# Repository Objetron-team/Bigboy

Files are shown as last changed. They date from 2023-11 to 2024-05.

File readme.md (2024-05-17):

# The Big boy
[Eurobot](https://www.coupederobotique.fr/wp-content/uploads/Eurobot2024_Rules_CUP_EN_FINAL.pdf)

## Mission
- Repot the plants and place them in cultivation
- Orient the solar panels
- Pollinate the plants
- Return to charge batteries
- Anticipate future crop yields

## Rules highlight
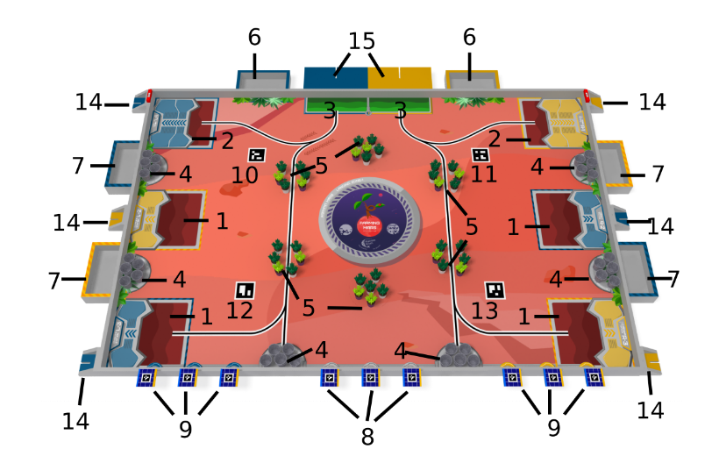
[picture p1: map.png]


|||
|-|-|
| 1) Departure/arrival and drop-off areas | 8) Solar panels |
| 2) Departure/arrival and reserved drop-off areas  | 9) Reserved solar panels |
| 3) Departure areas SIMA (ladybug hive) | 10) ArUco marker number 20 |
| 4) Pot supply | 11) ArUco marker number |
| 5) Plant supply | 12) ArUco marker number 22 |
| 6) Reserved planters | 13) ArUco marker number 23 |
| 7) Planters | 14) Fixed beacon supports |
| | 15) Remote computing area |

## Strategy

### Positionning

#### Bigboy
- Bigboy will be positioned in the departure area in a defined position.
- Bigboy will use its encoders to know its position.
- The mouvement will be determine by the system of tasks.

#### Ladybirds
- Ladybirds will wait for the Bigboy to send a signal to start moving.

### Plants

#### Storage
- Plants will be stored in the storage area of the robot.

#### Open/Close the claw
- Bigboy will open and close its claw to take/let plants in its storage area.
- The claws will be controlled by servo motor.

### Solar
- Not done in this project

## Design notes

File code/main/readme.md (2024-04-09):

# How does it work?

The robot has a BT module, we have encodded a series of actions.

```
b -> select the blue team
y -> select the yellow team

z -> start the sequence
s -> stop the sequence
n -> next move
```

Diagram

Diagram

The sequence is a predefined list of coordinate, a path is generated by a list of forward and rotation mouvement. The position of the pami is managed by two PID controller, for the distance made by the pami and its rotation. We can compute a target speed using the PIDs and the speed is fed to speed PID controller.
The pami stop when the goal is achieved or if an object is detected.

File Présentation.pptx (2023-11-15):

## Objetron

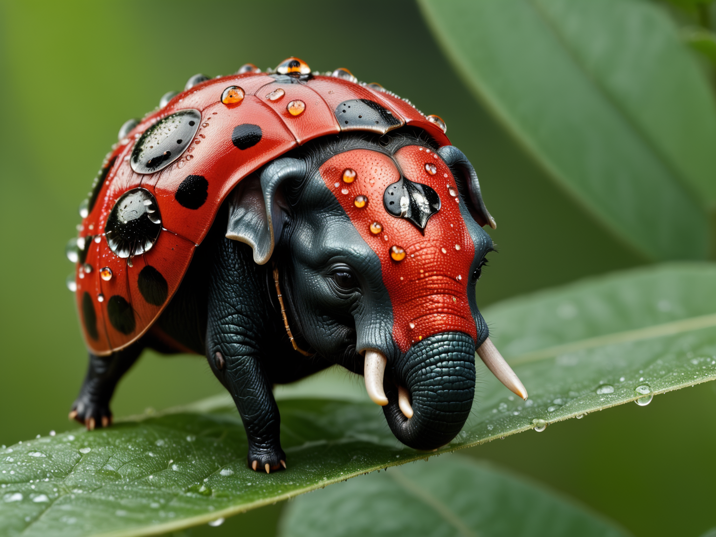
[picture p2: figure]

Florian Lebecque
Régis Irankunda
Rayhan Mezghani
Lancelot Neirinckx
Mathieu Surquin
Adrian Szydlowski

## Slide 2

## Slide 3

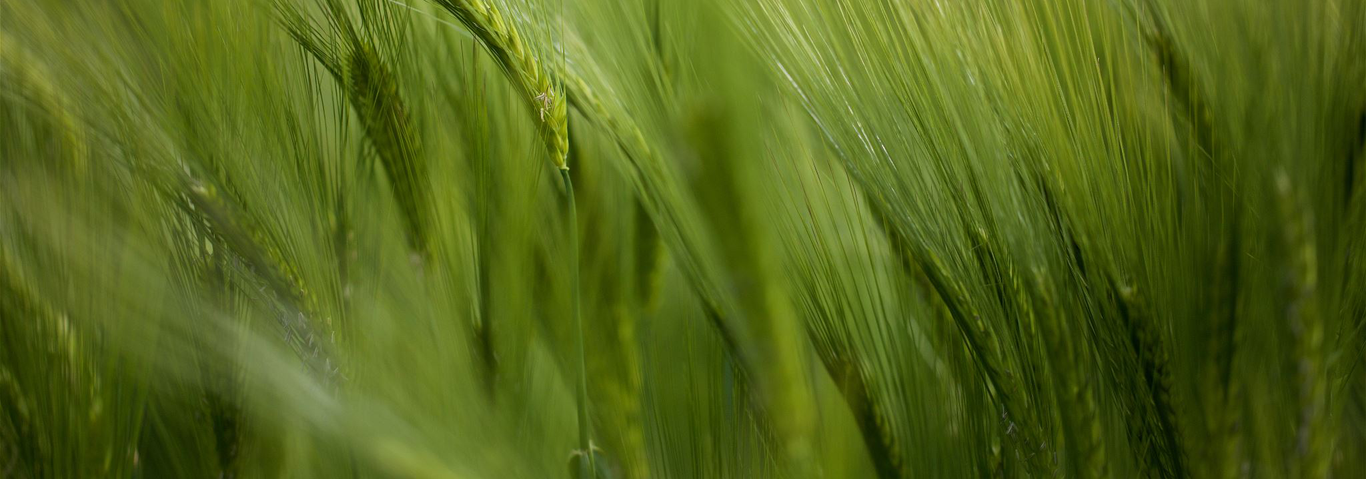
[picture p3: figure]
Gros plan d’orge dans la nature

Comment récolter et identifier les plantes

- Un système de courroie porteuse pour garder les plantes sur le robot
- Le robot identifie les plantes grâce à des capteurs RFID
- Les plantes sont stocker dans des zones différentes sur le robot selon leur type
- Mise en pot des plantes sera effectué sur le robot

## Stratégies

- Récolter plantes zone 5
- Récolter pots zone 4
- Identifier la plante
- Si 1 on prend plante fou dans le pot into zone commune
- Si 2 on prend la plante dans le pot into zone reservée
- Panneau solaire reservé, orientation avec un système de tige
- Panneau solaire non reservé, kinnect observation
- => en fonction du nombre de points
- 90s
- => Robot rentre à la zone de recharge
- => lancement des coccinelles

## Hardware

- Kinect xbox360
- Rails
- Moteurs
- Rasbery, Arduino
- Servo moteur
- Capteur rfid
- Roues
- Carte wifi ou arduino integré ESP32

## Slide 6

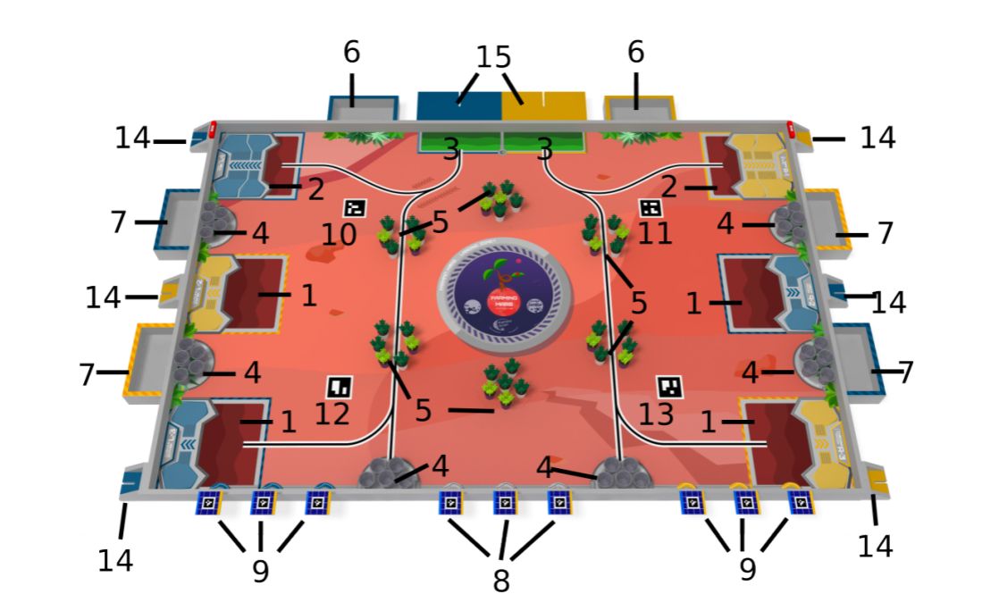
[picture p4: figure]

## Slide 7

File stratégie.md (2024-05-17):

# Stratégie EUROBOT
Dans ce document, nous allons décrire la stratégie de notre robot afin de ramener le plus de points possibles. La stratégie de notre robot peut se décomposer selon les étapes qui suivent.

## Plantes
La première étape va consister à la récolte des plantes. Bigoy démarre de la zone 1 pour l'équipe jaune ou zone 2 pour l'équipe bleue il ira ensuite rechercher les stocks de plantes afin de les emmener dans la zone de dépôt (1 et 2). Seules les plantes résistantes seront valides dans ces zones, et une plante dans la bonne zone donne 3 points.
=> 3*(2+2) = 12pts
### Plantes bonus
Le robot ira ensuite récuperer si possible les plantes du milieu de terrains et celles de l'adversaire si elles n'ont pas été touchées
=> 3*(2+2+2) = 18pts

## Panneaux solaires
Les panneaux solaires ne sont pas compris dans notre stratégie.

## PAMIS
L'étape suivante est attribuée aux PAMIs. À la 90ème seconde, les PAMIs entreront en contact avec une plante dans la zone de dépôt en moins de 10 secondes. Un PAMI qui est dans une zone de dépôt ramène 5 points, et s'il est en contact avec une plante, il rapporte 5 points de plus.
=> 5+5 = 10pts

## Retour à la base
À la fin de la manche, le robot retourne à sa zone de charge du coté adverse. Cette action donne 10 points.
=> 10 pts

## Affichage dynamique
Une dernière manière de marquer des points est de pouvoir prédire le score que le robot va faire durant le match. Nous avons décidé de le faire de manière dynamique via un écran OLED. À chaque tâche effectuée, le score s'incrémentera tout seul. Les points attribués pour cela sont donnés selon la formule suivante min(20-écarts/2; points réalisés).
=> 20 pts

## Conclusion
Bigboy et nos PAMIs utiliseront le même code avec le système de tâche. La détection de collision se fera à l'aide de capteurs ultrasons.
Si tout se passe comme prévu, nous devrions idéalement marquer 70 points.

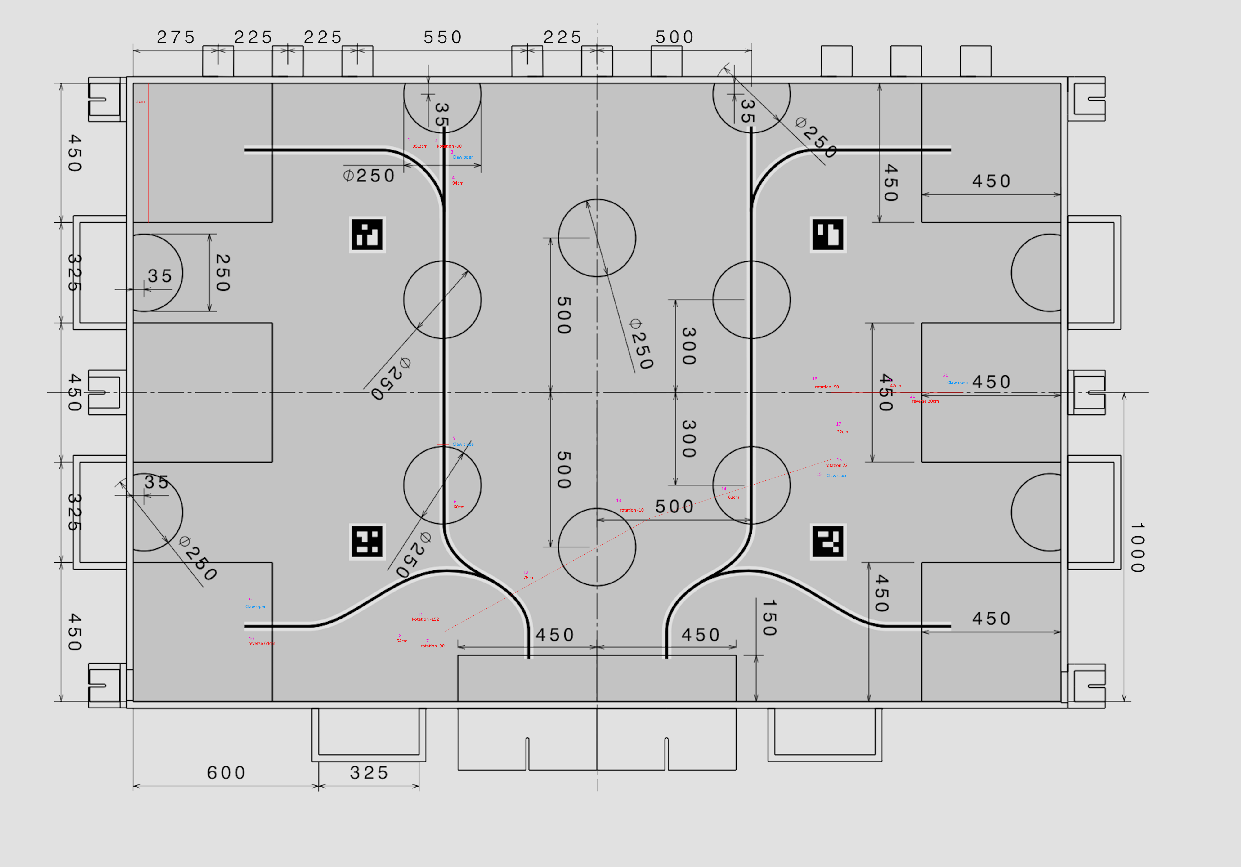
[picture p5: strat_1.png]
Map


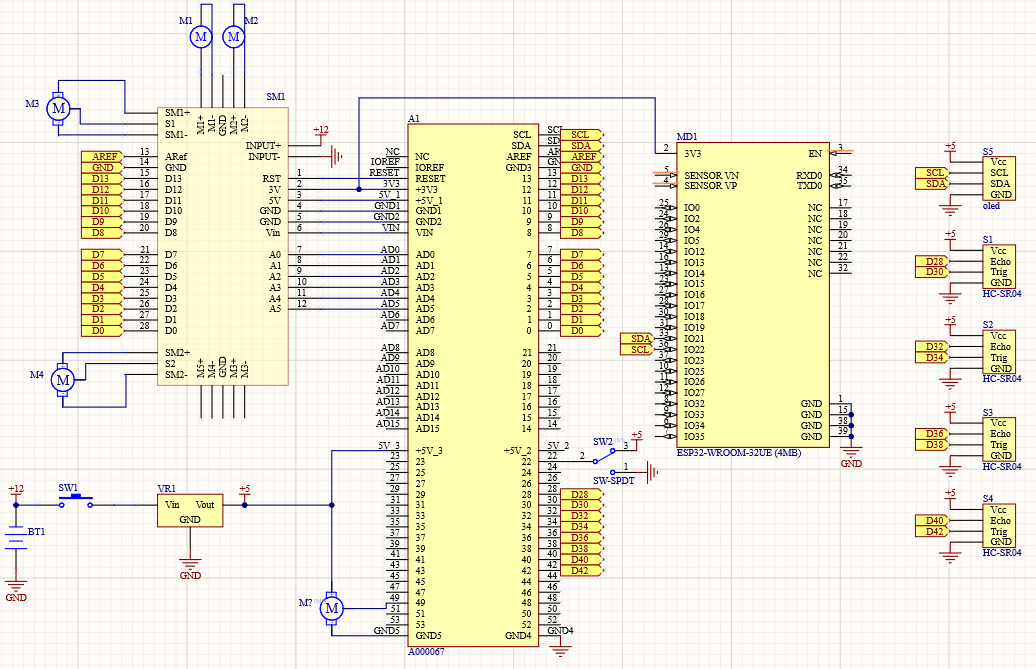
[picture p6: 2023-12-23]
electric_scheme.png

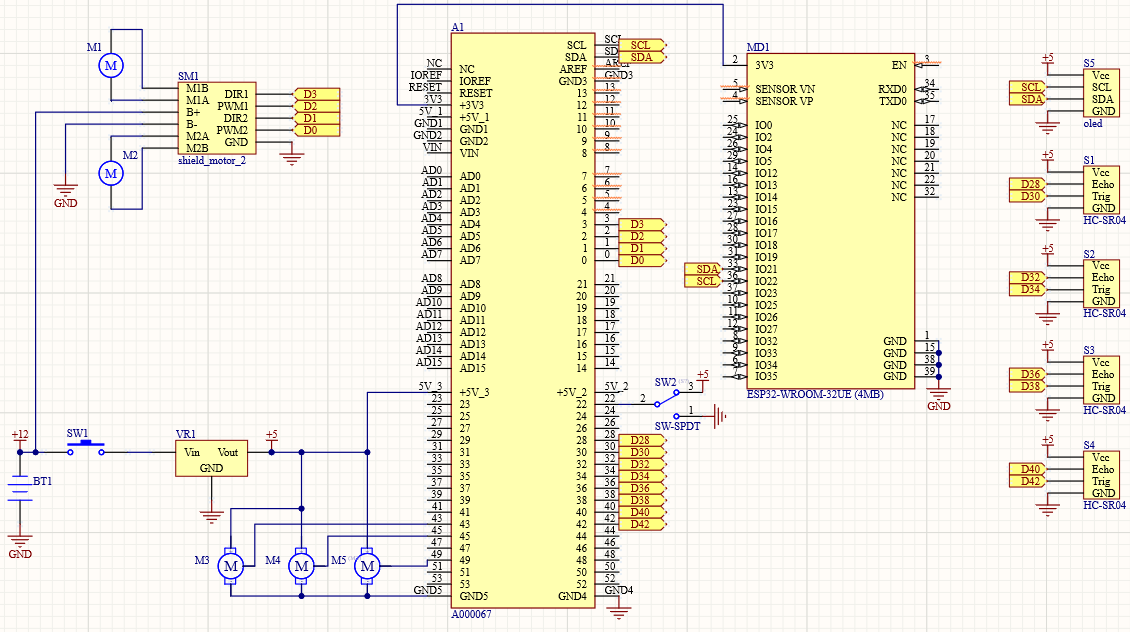
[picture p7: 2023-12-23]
electric_scheme_2.png

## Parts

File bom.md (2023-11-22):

# Bil of materials

## Miscellaneous

|Element|Name|target|Qty|Price|Link|
|-|-|-|-|-|-|
|Urgent stop| - | Lady + Big boy |4| - | - |
|Switch| 2 position | Lady + Big boy |4| - | - |

## Drive system

|Element|Name|target|Qty|Price|Link|
|-|-|-|-|-|-|
|Motor| moteur coci |Lady + Big boy|8|2.77€|https://fr.aliexpress.com/item/1005006027063973.html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|
|Chenilles|Zodiac MX8 MX6 Baracuda R0526100|Big boy|1|18.99€|https://www.amazon.fr/Chuancheng-Piscine-Zodiac-Baracuda-R0526100/dp/B07WZZRPDM|
|Encoder|LM393 Infrared Optocoupler Speed Sensor Module|Lady + Big Boy| 8|0.35|https://electropeak.com/ptocouple-optocounter-module

## Collision system

|Element|Name|target|Qty|Price|Link|
|-|-|-|-|-|-|
|Capteur Ultrason| HC-SR04 | Lady + Big boy |7|5.61€|https://www.mouser.be/ProductDetail/OSEPP-Electronics/HC-SR04?qs=wNBL%252BABd93PqZEhuhHkuOw%3D%3D|

## Solar rotator

|Element|Name|target|Qty|Price|Link|
|-|-|-|-|-|-|
|Servo motor| - | Big boy | 1 | - | - |
|Motor| - | Big boy | 1 | - | - |

## Beacon tower

|Element|Name|target|Qty|Price|Link|
|-|-|-|-|-|-|
|Raspberry| - | Beacon | 1 | - | - |
| Camera | - | Beacon | 2 | - | - |

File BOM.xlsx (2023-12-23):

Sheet: Sheet1
Element | Nom | Prix | Lien | Qnt
Capteur ultra-son | HC-SR04 | 5.61 € | https://www.mouser.be/ProductDetail/OSEPP-Electronics/HC-SR04?qs=wNBL%252BABd93PqZEhuhHkuOw%3D%3D | 7
Moteur cocci |  | 8.02 € | https://fr.aliexpress.com/item/1005006027063973.html?curPageLogUid=bDT0fOmhaEm0 | 1
servo-moteur |  |  |  | 2
moteur | GA12-N20 + encoder | 6 € | https://nl.aliexpress.com/item/1005004999529855.html | 8 | https://nl.aliexpress.com/item/1005002439195511.html?scm_id=1007.40050.362094.0&scm-url=1007.40050.362094.0
capteur anti-collision | VL53l0x |  | https://nl.aliexpress.com/item/1005006177829793.html?
Bouton d'arrêt d'urgence |  |  |  | 4
Switch |  |  |  | 4
Caméra |  |  |  | 1
raspberri pi |  |  |  | 1
Ecran LCD
Paire de chenilles | Zodiac MX8 MX6 Baracuda R0526100 | 18.99 | https://www.amazon.fr/Chuancheng-Piscine-Zodiac-Baracuda-R0526100/dp/B07WZZRPDM | 1 | 2.00 € | https://fr.aliexpress.com/item/1005006054487449.html?src=google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
Encodeur | LM393 Infrared Optocoupler Speed Sensor Module | 0.35 | https://electropeak.com/ptocouple-optocounter-module
 |  | €0.94 | https://fr.aliexpress.com/item/1005002105728736.html?scm_id=1007.40050.362094.0&scm-url=1007.40050.362094.0
Servo |  | 19.35 | https://befr.rs-online.com/web/p/servo-motors/7813046

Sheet: BigBoy
Elément | Nom | Quantité | Prix unité | Notes | Lien
Moteur + encodeur | JGB37-520 | 2 | 4 € | 12V, 1000 rpm, avec support (bracket) | JGB37-520 moteur à courant continu 6V12V avant et barrage vitesse réglable 6 tr/min-1590 tr/min kit de voiture intelligente avec roues - AliExpress (https://fr.aliexpress.com/item/1005005952624823.html?curPageLogUid=67h9Q2mkFTMm)
Capteur ultra-son | HC-SR04 | 4 | 5.61 € |  | https://www.mouser.be/ProductDetail/OSEPP-Electronics/HC-SR04?qs=wNBL%252BABd93PqZEhuhHkuOw%3D%3D
Bouton arret urgence |  | 1 |  | Fourni par le professeur
Batterie | LiPo 3S | 2 | 29 € |  | https://www.conrad.be/nl/p/tattu-lipo-accupack-11-1-v-2300-mah-aantal-cellen-3-45-c-softcase-xt60-1542437.html
5V buck converter | MINI560 | 1 | 1.13 € | PRO-5V | https://nl.aliexpress.com/i/1005001768198398.html?gatewayAdapt=glo2nld
Carte arduino | Arduino Mega | 1 | 45.01 € |  | https://www.mouser.be/ProductDetail/Arduino/A000067?qs=gMoqXxk%2F%2F5apEOlL63oO8Q%3D%3D
Shield moteur | L293D Motor shield | 1 | 6.99 € |  | https://www.amazon.fr/DollaTek-Shield-Expansion-Arduino-Duemilanove/dp/B07DK4NHRW
Carte raspberry pi | Raspberry Pi 4 | 1 | 32.55 € |  | https://www.mouser.be/ProductDetail/Raspberry-Pi/SC01929?qs=T%252BzbugeAwjg1Zb0G7gMcFw%3D%3D
Ecran OLED |  | 1 |  | fourni par le professeur
Servo rotation continue | Moteur DS04 NFC | 3 | 10 € |  | https://www.amazon.com.be/Moteur-DS04-NFC-moteur-rotation-continue/dp/B08KYCH3JJ
coupleur roue 6 mm |  | 4 | 1.50€ | 6mm | https://nl.aliexpress.com/item/1005005772748733.html?
Caméra | picam V3 | 1 | 30 € |  | https://www.arducam.com/product-category/cameras-for-raspberrypi/imx708-camera-module-3-for-pi/
tirette |  | 1 |  | Fourni par le professeur
switch |  |  |  | Fourni par le professeur (switch de stratégie couleur)
ESP32 | ESP32 | 1 | 8.37 |  | https://www.mouser.be/ProductDetail/Espressif-Systems/ESP32-C6-DevKitC-1-N8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

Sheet: PAMI
Elément | Nom | Quantité 1 robot | Quantité totale | Prix unité | Notes | Lien
LiPo 1300mAh 3s |  | 1 | 2 | 17.95 € | peut-être déjà des batteries similaires au labo | https://droneshop.nl/catalog/product/view/id/5600/s/tattu-funfly-1300mah-111v-100c-3s-lipo-battery/
Sac anti feu LiPo |  | 1 | 2 | 9.95 € | peut-être déjà disponible au labo | https://droneshop.nl/lipo-safe-bag-oplaadzak-small
Stop switch |  | 1 | 2
ESP32 wroom devkit |  | 1 | 2 | 8.99 € | Version avec le port "VIN" qui accepte 5 à 12V | https://www.otronic.nl/nl/esp32-wroom-4mb-devkit-v1-board-met-wifi-bluetooth.html
Driver moteurs | TB6612FNG | 1 | 2 | 7 € |  | https://www.tinytronics.nl/shop/nl/mechanica-en-actuatoren/motoraansturingen-en-drivers/dc-motoraansturingen-en-drivers/tb6612fng-easy-motor-driver
Moteurs + encodeurs | GB12-N20B | 2 | 4 | 6 € | 310rpm 6V | https://nl.aliexpress.com/item/32857563560.html?
roue 3mm type D |  | 2 | 4 | 0.24 € |  | https://nl.aliexpress.com/item/32809043739.html?
switch 2 position |  | 1 | 2
roue à bille metal 3/8" | pololu 951 | 1 | 2 | 3.34 € |  | https://www.vanallesenmeer.nl/Ball-Caster-with-3/8%E2%80%B3-Metal-Ball-Pololu-951
HC-SR04 |  | 1 | 2 |  | surement disponible au labo
Buck 11.1V -> 6V | D36V28F6 | 1 | 2 | 11.95 € |  | https://www.vanallesenmeer.nl/6V,-2.7A-Step-Down-Voltage-Regulator-D36V28F6-Pololu-3783

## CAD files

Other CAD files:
Prototype v1.f3d

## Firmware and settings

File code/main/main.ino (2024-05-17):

#define SAMPLE_TIME 15

#define IS_MAIN true
#define PAMI_TYPE 0 // 0 -> noir 1 -> gris


#if IS_MAIN
    
    #define DEATH_TIME 90 // in s
    #define LEVEL_PIN 23
    
    #include "settings/main/motor_def.h"
    #include "settings/main/drive_def.h"
    #include "settings/main/radar.h"
    #include "settings/main/claw.h"
    #include "settings/main/arm.h"
#else
    #define DEATH_TIME 10 // in s
        
    #include "settings/pami/motor_def.h"
    #include "settings/pami/drive_def.h"
    #include "settings/pami/radar.h"

#endif

#include "PIDMotor.hpp"
#include "DriveControler.hpp"
#include "PositionControler.hpp"
#include "TaskControler.hpp"
#include "Arm.hpp"
#include "Claw.hpp"
#include "Radar.hpp"
#include "PositionTaskBuilder.hpp"

#include "ESPNowStruct.hpp"
#include "ESPNowMaster.hpp"
#include "ESPNowSlave.hpp"

#include <LCD-I2C.h>
#include <Wire.h>

LCD_I2C lcd(0x27, 16, 2);
int points = 0;

#define RXp2 16
#define TXp2 17

// variable used for communication
const int BUFFER_SIZE = 64; // Adjust the buffer size as needed
char buffer[BUFFER_SIZE];
int bufferIndex = 0;
int number = 100;
// variable used for competition
bool competition = true;
int ok = 1;

PIDMotor motorL(MOTOR_L_PIN_1, MOTOR_L_PIN_2, MOTOR_ACCELERATION, MOTOR_MAX_SPEED, MOTOR_MIN_SPEED, MOTOR_THRESHOLD_SPEED, PAMI_DUAL_MODE);
PIDMotor motorR(MOTOR_R_PIN_1, MOTOR_R_PIN_2, MOTOR_ACCELERATION, MOTOR_MAX_SPEED, MOTOR_MIN_SPEED, MOTOR_THRESHOLD_SPEED, PAMI_DUAL_MODE);

ValueConverter valueConverter(ENCODER_RESOLUTION, WHEEL_DIAMETER, WHEEL_DISTANCE);

DriveControler driveControler(& motorL, & motorR);
PositionControler positionControler(& driveControler, ENCODER_RESOLUTION, WHEEL_DIAMETER, WHEEL_DISTANCE);

TaskControler taskControler(& positionControler, & driveControler, & valueConverter);

PositionTaskBuilder positionTaskBuilder(& positionControler, & driveControler, & valueConverter);

#if IS_MAIN
    Arm myArm(PIN_ARM, ARM_TIME);
    Claw myClaw(PIN_CLAW_1, PIN_CLAW_2, CLAW_TIME);
    ESPNowMaster espNowMaster;

#else
    Radar radar(TRIGGER_PIN, ECHO_PIN);
    ESPNowSlave espNowSlave(& taskControler, & positionTaskBuilder);

#endif

void setup()
{
    Serial.begin(115200);
    
    #if IS_MAIN
        
        pinMode(LEVEL_PIN, INPUT);
    
    if (digitalRead(LEVEL_PIN) == HIGH) //bleu
    {
        command_data pami_gris_cmd;
        pami_gris_cmd.cmd_1 = BLUE_ONE;
        pami_gris_cmd.cmd_2 = AUTO_ON;
        pami_gris_cmd.cmd_3 = START;
        
        uint8_t mac_gris[] = {0xE4, 0x65, 0xB8, 0x79, 0x83, 0x14};
        
        slave_data pami_gris;
        memcpy(pami_gris.mac_address, mac_gris, 6);
        pami_gris.cmd_data = pami_gris_cmd;
        
        command_data pami_noir_cmd;
        pami_noir_cmd.cmd_1 = BLUE_TWO;
        pami_noir_cmd.cmd_2 = AUTO_ON;
        pami_noir_cmd.cmd_3 = START;
        
        uint8_t mac_noir[] = {0xE4, 0x65, 0xB8, 0x76, 0x94, 0x44};
        
        slave_data pami_noir;
        memcpy(pami_noir.mac_address, mac_noir, 6);
        pami_noir.cmd_data = pami_noir_cmd;
        
        
        espNowMaster.AddSlave(pami_gris);
        espNowMaster.AddSlave(pami_noir);
        
    }
    else    //yellow
    {
        command_data pami_gris_cmd;
        pami_gris_cmd.cmd_1 = YELLOW_ONE;
        pami_gris_cmd.cmd_2 = AUTO_ON;
        pami_gris_cmd.cmd_3 = START;
        
        uint8_t mac_gris[] = {0xE4, 0x65, 0xB8, 0x79, 0x83, 0x14};
        
        slave_data pami_gris;
        memcpy(pami_gris.mac_address, mac_gris, 6);
        pami_gris.cmd_data = pami_gris_cmd;
        
        command_data pami_noir_cmd;
        pami_noir_cmd.cmd_1 = YELLOW_TWO;
        pami_noir_cmd.cmd_2 = AUTO_ON;
        pami_noir_cmd.cmd_3 = START;
        
        uint8_t mac_noir[] = {0xE4, 0x65, 0xB8, 0x76, 0x94, 0x44};
        
        slave_data pami_noir;
        memcpy(pami_noir.mac_address, mac_noir, 6);
        pami_noir.cmd_data = pami_noir_cmd;
        
        
        espNowMaster.AddSlave(pami_gris);
        espNowMaster.AddSlave(pami_noir);
    }
    
    // Initialize the ESPNow master
    espNowMaster.Init();
    // Initialize the claw
    myClaw.Init();
    // Initialize the LCD
    pinMode(35, INPUT);
    lcd.begin();
    lcd.display();
    lcd.backlight();
    lcd.setCursor(0, 0);
    lcd.print("Nombre de points:");
    lcd.setCursor(0, 1);
    lcd.print("32");
    // Initialize the arm
    myArm.Init();
    // Initialize the radar transmission
    Serial2.begin(9600, SERIAL_8N1, RXp2, TXp2);
    
    #else
        radar.Init();
        espNowSlave.Init();
        driveControler.AddRadar( & radar, FRONT);
    #endif
    
    // Motor setup
    motorL.InitEncoder(ENCODER_L_PIN_A, ENCODER_L_PIN_B, ENCODER_MAX_FREQ_L, ENCODER_RESOLUTION, WHEEL_DIAMETER);
    motorR.InitEncoder(ENCODER_R_PIN_A, ENCODER_R_PIN_B, ENCODER_MAX_FREQ_R, ENCODER_RESOLUTION, WHEEL_DIAMETER);
    
    // PID setup
    motorL.InitPID(LS_PID_KP, LS_PID_KI, LS_PID_KD, SAMPLE_TIME);
    motorR.InitPID(RS_PID_KP, RS_PID_KI, RS_PID_KD, SAMPLE_TIME);
    
    // DriveControler setup
    driveControler.InitPid(DISTANCE_KP, DISTANCE_KI, DISTANCE_KD, ANGLE_KP, ANGLE_KI, ANGLE_KD, SAMPLE_TIME);
    
    taskControler.SetAutoMode(false);
    
}

int processBuffer()
{
    int parsed_number = 0;
    // Process the data stored in the buffer
    // For example, you can print it or perform any other desired operation
    for (int i = 0; i < bufferIndex; i++)
    {
        if (buffer[i] == '\n')
        {
            // If newline character is encountered, print the message and reset buffer
            
            parsed_number = atoi(buffer); // Convert the buffer content to an integer
            if (parsed_number != 0)
            {
                number = parsed_number; // Update the global variable only if a valid number is parsed
            }
            
            if (number < 20)
            {
                driveControler.UrgentStop();
            }
            
            // Move remaining data to the beginning of the buffer
            memmove(buffer, buffer + i + 1, bufferIndex - i - 1);
            bufferIndex -= i + 1;
            i = -1; // Reset i to start from the beginning of the buffer
        }
    }
    return parsed_number;
}

void handleCompetitionTasks(){
    // Start the communication with the ESPNow slaves
    espNowMaster.Start();
    
    // part 1 -> go to the line and rotate -> open claw
    taskControler.AddTask(new ForwardTask(& driveControler, & valueConverter, 95));
    taskControler.AddTask(new RotationTask(& driveControler, & valueConverter, -90));
    taskControler.AddTask(new ClawTask(& myClaw, OPEN));
    
    // part 2 -> Recolt the flowers and go to dropzone
    taskControler.AddTask(new ForwardTask(& driveControler, & valueConverter, 95)); 
    taskControler.AddTask(new ClawTask(& myClaw, CLOSE));
    taskControler.AddTask(new RotationTask(& driveControler, & valueConverter, -50)); 
    taskControler.AddTask(new ForwardTask(& driveControler, & valueConverter, 65 ));
    
    // part 3 -> Cash the flowers
    taskControler.AddTask(new ClawTask(& myClaw, OPEN));
    taskControler.AddTask(new ReverseTask(& driveControler, & valueConverter, 30)); 
    
    // part 4 -> Go to next circle
    taskControler.AddTask(new RotationTask(& driveControler, & valueConverter, 140));
    taskControler.AddTask(new ForwardTask(& driveControler, & valueConverter, 76)); 
    taskControler.AddTask(new RotationTask(& driveControler, & valueConverter, 45));
    taskControler.AddTask(new ForwardTask(& driveControler, & valueConverter, 53));
    taskControler.AddTask(new ClawTask(& myClaw, CLOSE));
    
    // part 5 -> Align for cash in
    taskControler.AddTask(new RotationTask(& driveControler, & valueConverter, 60));
    taskControler.AddTask(new ForwardTask(& driveControler, & valueConverter, 35));
    taskControler.AddTask(new RotationTask(& driveControler, & valueConverter, -90));
    taskControler.AddTask(new ForwardTask(& driveControler, & valueConverter, 75));
    taskControler.AddTask(new ClawTask(& myClaw, OPEN));
    taskControler.AddTask(new ReverseTask(& driveControler, & valueConverter, 15));
    
    // Set the task controler to auto mode and start it
    taskControler.SetAutoMode(true);
    taskControler.Start();
    ok = 0;
}
void loop()
{
    #if IS_MAIN
        // Check if the competition has started
        while(digitalRead(35) != LOW) {
            Serial.println("attente");
        }
        
        if (competition == true && ok ==  1) {
            handleCompetitionTasks();        
        }
        
        while(Serial2.available() > 0)
        {
            char incomingByte = Serial2.read();
            
            // Store incoming byte in the buffer
            buffer[bufferIndex++] = incomingByte;
            
            // Check if the buffer is full
            if (bufferIndex >= BUFFER_SIZE)
            {
                processBuffer(); // Process the buffer when it's full
            }
        }
        
        // Process remaining data in the buffer
        if (bufferIndex > 0)
        {
            processBuffer();
        }
       
        // Update to see if the time is up
        espNowMaster.Update();
    #endif
    
    taskControler.Update();
    
    delay(5);
}

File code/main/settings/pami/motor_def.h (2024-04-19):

// Motor definition

//  Left motor pins
#define MOTOR_L_PIN_1 32
#define MOTOR_L_PIN_2 33

//  Right motor pins
#define MOTOR_R_PIN_1 25
#define MOTOR_R_PIN_2 26

//  Global motor parameters
#define MOTOR_ACCELERATION 75
#define MOTOR_MAX_SPEED 100
#define MOTOR_MIN_SPEED 0
#define MOTOR_THRESHOLD_SPEED 2

//  Dual mode, depending on the motor driver
#define PAMI_DUAL_MODE true

// Encoder definition

#define ENCODER_L_PIN_A 18
#define ENCODER_L_PIN_B 19

#define ENCODER_R_PIN_A 39
#define ENCODER_R_PIN_B 36

#if PAMI_TYPE == 0
// PAMI NOIRE
#define ENCODER_RESOLUTION 1786 // pulses per revolution
#define ENCODER_MAX_FREQ_L 6400 // Hz
#define ENCODER_MAX_FREQ_R 6400 // Hz
#define WHEEL_DIAMETER 0.035    // meters
#define WHEEL_DISTANCE 0.12 / 2 // meters
#else
// PAMI GRIS
#define ENCODER_RESOLUTION 3570  // pulses per revolution
#define ENCODER_MAX_FREQ_L 11032 // Hz
#define ENCODER_MAX_FREQ_R 10125 // Hz
#define WHEEL_DIAMETER 0.035     // meters
#define WHEEL_DISTANCE 0.12 / 2  // meters
#endif

#define MAX_SPEED_PULSE ((ENCODER_MAX_FREQ_L + ENCODER_MAX_FREQ_R) / 2) * (MOTOR_MAX_SPEED / 100.0)

// PID definition

#define LS_PID_KP 1
#define LS_PID_KI 0
#define LS_PID_KD 0

#define RS_PID_KP 1
#define RS_PID_KI 0
#define RS_PID_KD 0

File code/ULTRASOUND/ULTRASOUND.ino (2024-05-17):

// Nombre total de pins echo utilisées
const int NUM_ECHO_PINS = 9;

// Tableau des pins Echo
const int echoPins[NUM_ECHO_PINS] = {5, 6, 7, 8, 9, 10, 11, 12, 13};

// Pin Trigger
const int trigPin = 3;

// Définir le timeout pour la mesure de la distance
#define MEASURE_TIMEOUT 25000UL

// Initialisation des pins et de la communication série
void setup() {
  // Configurer la pin trig en sortie
  pinMode(trigPin, OUTPUT); 

  // Configurer toutes les pins echo en entrée
  for (int i = 0; i < NUM_ECHO_PINS; i++) {
    pinMode(echoPins[i], INPUT);
  }

  // Initialiser la communication série à 9600 baud
  Serial.begin(9600);
}

// Fonction pour obtenir la distance mesurée par un capteur ultrason
float getDistance(int echoPin) {
  // Envoyer une impulsion ultrason
  digitalWrite(trigPin, LOW);
  delayMicroseconds(2);
  digitalWrite(trigPin, HIGH);
  delayMicroseconds(10);
  digitalWrite(trigPin, LOW);

  // Mesurer la durée de l'impulsion retournée
  float duration = pulseIn(echoPin, HIGH, MEASURE_TIMEOUT);

  // Calculer la distance en centimètres
  float distance = (duration * 0.0343) / 2;

  // Si la distance est 0 (erreur de mesure), assigner une valeur "infinie"
  if (distance == 0) {
    distance = 100000; 
  }
  
  return distance;
}

// Fonction pour imprimer la distance mesurée par un capteur ultrason
void printDistance(int echoPin) {
  float distance = getDistance(echoPin);
  Serial.print("Pin ");
  Serial.print(echoPin);
  Serial.print(": ");
  Serial.println(distance);
}

// Fonction pour déboguer les distances mesurées par tous les capteurs
void debugDistances() {
  for (int i = 0; i < NUM_ECHO_PINS; i++) {
    printDistance(echoPins[i]);
  }
}

// Boucle principale
void loop() {
  float distances[NUM_ECHO_PINS];

  // Mesurer les distances pour toutes les pins echo
  for (int i = 0; i < NUM_ECHO_PINS; i++) {
    distances[i] = getDistance(echoPins[i]);
  }

  // Trouver la distance minimale mesurée
  float minDistance = distances[0];
  for (int i = 1; i < NUM_ECHO_PINS; i++) {
    if (distances[i] < minDistance) {
      minDistance = distances[i];
    }
  }

  // Imprimer la distance minimale qui sera lue par l'ESP32
  Serial.println(minDistance);

  // Décommenter pour déboguer les distances mesurées par tous les capteurs
  // debugDistances();
}

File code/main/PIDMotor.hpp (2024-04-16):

/*
    Class to control a motor with a PID controller and an encoder.
        - Control the motor is used with a ramp to avoid high current draw
        - The encoder is used to get the speed of the motor
        - The PID controller is used to control the speed of the motor

        In dual Mode,
            - The motor is controlled with two pins, one for the speed in one direction and one for the speed in the other direction
            - direction_pin -> speed in forward direction
            - speed_pin -> speed in backward direction
                ! both pin are analogWrite pins

        In single Mode,
            - The motor is controlled with one pin for the speed and one pin for the direction
            - direction_pin -> direction of the motor
                ! direction_pin is a digitalWrite pin   -> HIGH for forward, LOW for backward
            - speed_pin -> speed of the motor
                ! speed_pin is an analogWrite pin
*/

#pragma once

#include <Arduino.h>;
#include <ESP32Encoder.h>
#include <PID_v1.h>

#define NBR_OF_SPEED_MEASUREMENTS 10
#define PID_ENABLE false

class PIDMotor
{
private:
    // Type of driver
    bool dual_input;

    // Motor pins
    int pin_direction;
    int pin_speed;

    // Motor parameters
    double current_speed;
    double threshold_speed;
    double min_speed;
    double max_speed;

    // Motor timing
    long last_update_time;
    double max_acceleration; // in power/seconde -> 0.1 is 10% increase per seconde

    // Encoder
    ESP32Encoder encoder;

    int MAX_FREQUENCY = 1000; // in Hz
    int PULSES_PER_TURN = 1;
    double wheel_diameter = 1; // in meter

    double VFilt = 0;
    double VPrev = 0;
    double speed_measurements[NBR_OF_SPEED_MEASUREMENTS];

    long last_encoder_time;
    long last_encoder_value;

    // PID
    PID *pid;

    double setpoint, input, output;

    void SetSpeed_with_ramp(double target)
    {
        // Increase or decrease the current speed to reach the target speed by the max acceleration
        double delta_time = (millis() - last_update_time) / 1000.0;
        last_update_time = millis();

        int target_sign = abs(target) / target;

        if (abs(target) < threshold_speed)
        {
            target = 0;
        }

        if (abs(target) > max_speed)
        {
            target = target_sign * max_speed;
        }

        double delta_speed = delta_time * max_acceleration;

        if (target > current_speed)
        {
            current_speed += delta_speed;
            if (current_speed > target)
            {
                current_speed = target;
            }
        }
        if (target < current_speed)
        {
            current_speed -= delta_speed;
            if (current_speed < target)
            {
                current_speed = target;
            }
        }

        SetMotorSpeendAndDir(current_speed);
    }

    void SetMotorSpeendAndDir(double speed)
    {

        if (abs(speed) < min_speed && speed != 0)
        {
            speed = speed / abs(speed) * min_speed;
        }

        // Convert the speed in % to a value between 0 and 255
        double value = abs(speed) * 255 / 100.0;

        if (dual_input)
        {

            // in dual_input mode, the pin_direction is used a a second speed pin, the two speed pins are used to control the speed of the motor and direction.
            // pin_direction -> speed in forward direction
            // pin_speed -> speed in backward direction

            if (speed < 0)
            {
                analogWrite(pin_speed, value);
                analogWrite(pin_direction, 0);
            }
            else if (speed > 0)
            {
                analogWrite(pin_speed, 0);
                analogWrite(pin_direction, value);
            }
            else
            {
                analogWrite(pin_speed, 0);
                analogWrite(pin_direction, 0);
            }

            return;
        }

        if (speed < 0)
        {
            digitalWrite(pin_direction, HIGH);
        }
        if (speed >= 0)
        {
            digitalWrite(pin_direction, LOW);
        }

        analogWrite(pin_speed, value);
    }

public:
    PIDMotor(int pin_direction, int pin_speed, double max_acceleration, double max_speed, double min_speed, double threshold_speed, bool dual_input)
    {
        this->pin_direction = pin_direction;
        this->pin_speed = pin_speed;
        this->max_acceleration = max_acceleration;
        this->threshold_speed = threshold_speed;
        this->min_speed = min_speed;
        this->max_speed = max_speed;
        this->dual_input = dual_input;
        this->current_speed = 0;
        this->last_update_time = millis();
        pinMode(pin_direction, OUTPUT);
        pinMode(pin_speed, OUTPUT);
    }

    void InitEncoder(int pinA, int pinB, int max_frequency, int pulses_per_turn, double wheel_diameter)
    {
        encoder.attachFullQuad(pinA, pinB);
        encoder.setCount(0);

        this->MAX_FREQUENCY = max_frequency;
        this->PULSES_PER_TURN = pulses_per_turn;
        this->wheel_diameter = wheel_diameter;
    }

    void InitPID(double Kp, double Ki, double Kd, double sample_time_ms)
    {
        pid = new PID(&input, &output, &setpoint, Kp, Ki, Kd, DIRECT);
        pid->SetMode(AUTOMATIC);
        pid->SetOutputLimits(-100, 100);
        pid->SetSampleTime(sample_time_ms);
    }

    void SetSpeed(double speed)
    {
        setpoint = speed; // Set the setpoint of the PID, in % of the max speed
    }

    double GetSpeed()
    {
        long currentMicros = micros();
        long currentCount = encoder.getCount();

        long deltaMicros = currentMicros - last_encoder_time;
        long deltaCount = currentCount - last_encoder_value;

        last_encoder_time = currentMicros;
        last_encoder_value = currentCount;

        if (deltaMicros == 0)
        {
            return 0;
        }

        double speed = deltaCount * 1000000 / deltaMicros;

        // add low pass filter 25hz before adding to the array
        this->VFilt = 0.854 * this->VFilt + 0.0728 * speed + 0.0728 * this->VPrev;
        this->VPrev = speed;

        for (int i = 0; i < NBR_OF_SPEED_MEASUREMENTS - 1; i++)
        {
            speed_measurements[i] = speed_measurements[i + 1];
        }

        speed_measurements[NBR_OF_SPEED_MEASUREMENTS - 1] = VFilt;

        double sum = 0;
        for (int i = 0; i < NBR_OF_SPEED_MEASUREMENTS; i++)
        {
            sum += speed_measurements[i];
        }

        return sum / NBR_OF_SPEED_MEASUREMENTS;
    }

    double GetSpeedRelative()
    {

        double absolute_relative_speed = GetSpeed() / MAX_FREQUENCY * 100;

        double real_relative_speed = absolute_relative_speed / (max_speed / 100);

        return real_relative_speed;
    }

    double GetSpeedMeterPerSeconde()
    {
        return GetSpeed() * wheel_diameter * PI / PULSES_PER_TURN;
    }
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

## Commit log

2023-11-22 add bom
    [BOM.xlsx]
2023-11-22 bom md
2023-12-21 MAJ BOM
    [BOM.xlsx]
2023-12-23 MAJ files
    [BOM.xlsx]
2024-02-15 Add pami code to bigboy; todo -> rewrite the encoder
2024-02-15 Update motor and encoder class to work with new encoder and new motor
2024-02-16 fixe encoder
2024-02-20 add support for DUAL motor input
2024-02-20 fixe control motor
2024-02-20 parametrize encoder parameters
2024-02-28 debug and pid tning
2024-03-01 disable the Two cable component
2024-03-01 change pin and motor parameters
2024-03-22 Add claw classs
2024-03-22 fixe bugs with servo
2024-03-22 Set the encoder resolution
2024-03-22 Define and use Claw for the big boi only
2024-03-22 remove claw for pami
2024-03-23 Add missing value and change config
    [motor_def.h]
2024-03-25 fixe missing data for position controller
    [main.ino]
2024-03-26 update pami drive controller PID
2024-03-29 block motor while waiting
2024-03-29 Fix output pin
2024-03-29 fixe point in main
    [main.ino]
2024-04-01 change PID settings
2024-04-02 Add ultrasons, TODO: Fix UrgentStop
    [drive_def.h, main.ino, motor_def.h]
2024-04-02 ServoMoteur Fixed, TODO: UrgentStop working 1/10 times
    [main.ino]
2024-04-02 fix open/closed claw, TODO: NEED DEBUG DE L'URGENT STOP FLORIAN
2024-04-05 update PID value for drive controller
2024-04-09 fix miss sized array
    [main.ino]
2024-04-09 print TTL in debug
2024-04-09 fix ultrasons, add arm class
    [drive_def.h, main.ino, motor_def.h]
2024-04-09 claw execution
2024-04-10 change point and and change motor parameters
2024-04-16 allow to disable PID of motors
2024-04-18 fix Big robot path, add LCD, change parameter to make it work, TODO:Task for claw, Task for arm, Task for backward, TODO2: Add new ultrasound in arduino
    [MoveTask.hpp, PIDMotor.hpp, RotateTask.hpp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]
2024-04-19 Increase PID angle for pami
2024-04-19 Add debug and fix distance error
    [MoveTask.hpp, ReverseTask.hpp]
2024-04-19 increase angle PID
2024-04-19 add claw operationelle
2024-04-20 change how the claw task is used
2024-04-20 Clean and rework strat
    [main.ino]
2024-04-22 add arduino ultrasound code
